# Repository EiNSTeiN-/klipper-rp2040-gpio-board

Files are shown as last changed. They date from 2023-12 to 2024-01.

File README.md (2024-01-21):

# Klipper RP2040 GPIO board

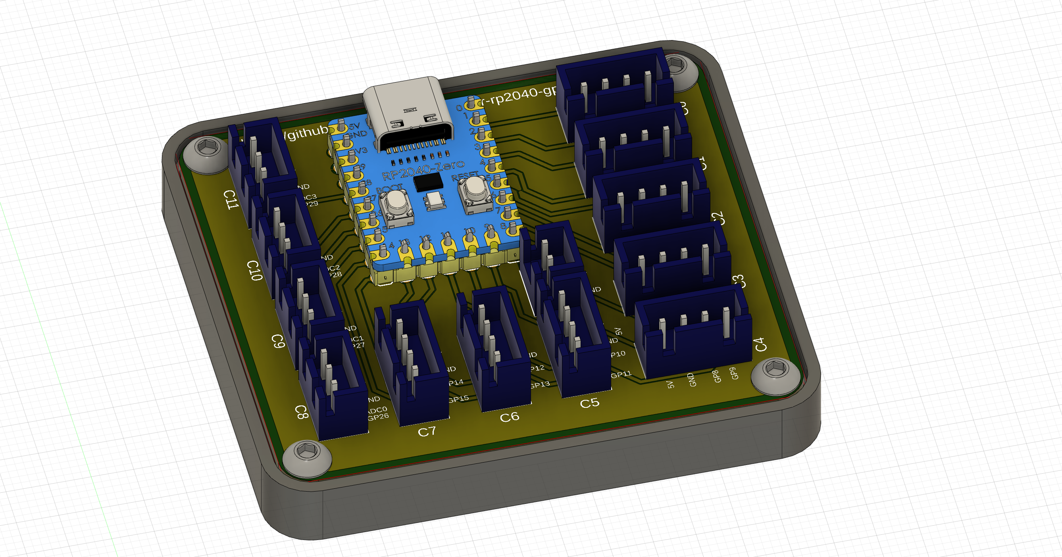
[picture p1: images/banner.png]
CAD Preview


This is a small board that makes it convenient to connect additional sensors to your 3D printer running klipper, based on [RP2040-Zero](https://www.waveshare.com/wiki/RP2040-Zero). It exposes all available analog pins to 4-pin JST-XH headers, and digital pins to 3-pin JST-XH headers.

Features:
* Up to 20 analog pins (buttons, encoders, etc)
* Up to 4 digital pins (servos, hall sensors, thermistors, etc)
* 2 x SPI bus available
* 2 x I2C bus available

## BOM

| Name | Quantity | Description |
|---|---|---|
| PCB | 1 | Order online from your favorite PCB supplier (PCBWay, JLCPCB, etc). |
| RP2040-Zero | 1 | From [Waveshare](https://www.waveshare.com/rp2040-zero.htm) (also available on Aliexpress).
| JST-XH 4-pin | 8 | |
| JST-XH 3-pin | 4 | |
| JST-XH 2-pin | 1 | |
| M3 x heat set insert | 4 | Optional, only needed for the case. |
| M3 x 6mm | 4 | BHCS or SHCS screws. Optional, only needed for the case. |
| Case_bottom.stl | 1 | Optional, print if needed. |

## Klipper installation

Compile Klipper for the RP2040 board. The commands below are intended to be run on your printer host:
```sh
git clone --depth 1 --single-branch https://github.com/Klipper3d/klipper.git ~/klipper-rp2040-gpio
cd ~/klipper-rp2040-gpio
~/klippy-env/bin/python scripts/make_version.py `hostname`
# v0.11.0-146-ge2d7c598-mainsailos
make menuconfig
#                 Klipper Firmware Configuration
#  [*] Enable extra low-level configuration options
#      Micro-controller Architecture (Raspberry Pi RP2040)  --->
#      Bootloader offset (No bootloader)  --->
#      Flash chip (W25Q080 with CLKDIV 2)  --->
#      Communication interface (USB)  --->
#      USB ids  --->
#  ()  GPIO pins to set at micro-controller startup
make -j4
#   (...lots of output...)
#   Creating uf2 file out/klipper.uf2
ls -alh /dev/serial/by-id/usb-*
# lrwxrwxrwx 1 root root 13 Dec 18 15:53 /dev/serial/by-id/usb-RPI_rp2040_E66130100F5E3838-if00 -> ../../ttyACM1
make flash FLASH_DEVICE=/dev/serial/by-id/usb-RPI_rp2040_E66130100F5E3838-if00
ls -alh /dev/serial/by-id/usb-Klipper_rp2040*
# lrwxrwxrwx 1 root root 13 Dec 18 15:53 /dev/serial/by-id/usb-Klipper_rp2040_E66130100F5E3838-if00 -> ../../ttyACM1
```

#### Troubleshooting

* Problem: After flashing the board works fine, but after disconnecting/reconnecting the board it does not boot anymore.
* Solution: Run `make menuconfig` and select `Flash chip (GENERIC_03H with CLKDIV 4)`. See [this issue](https://github.com/raspberrypi/pico-sdk/issues/1304).

## Configuration example

Your specific configuration depends on what is connected to the gpio pins. Example of a minimal configuration:

```ini
[mcu rp2040]
# find with: ls -alh /dev/serial/by-id/usb-Klipper_rp2040*
serial: /dev/serial/by-id/usb-Klipper_rp2040_E66130100F5E3838-if00

[neopixel rp2040_rgb]
pin: rp2040:gpio16
#color_order: GRB
initial_GREEN: 1.0

####
# Add sensors below:

[gcode_button my_button]
pin: ~rp2040:gpio4
press_gcode:
  RESPOND TYPE=command MSG='GP4 pressed'

[pwm_tool my_tool]
pin: rp2040:gpio26
```

Pin `gpio16` can only be used as a neopixel since it is soldered to the RP2040-Zero.

Consult [klipper's configuration reference](https://www.klipper3d.org/Config_Reference.html) for information on how to configure specific sensors with klipper.

## Pinout

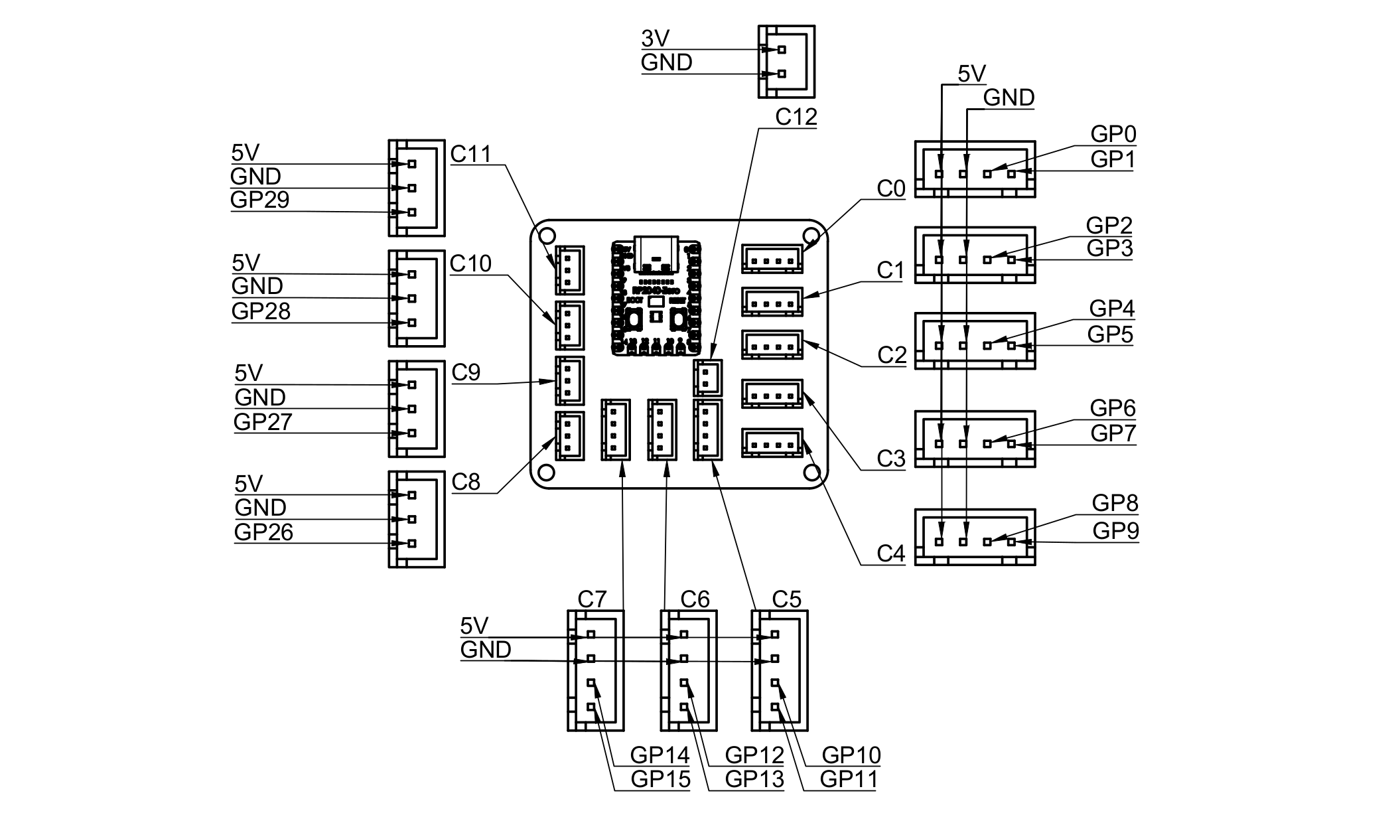
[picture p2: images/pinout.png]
Pinout


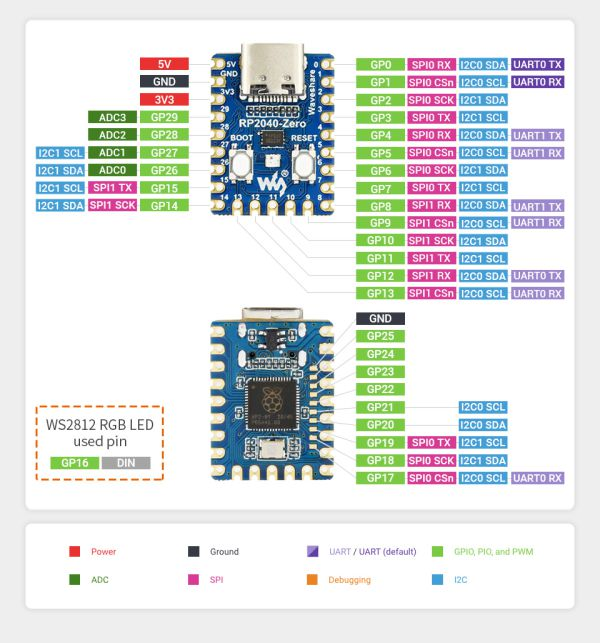
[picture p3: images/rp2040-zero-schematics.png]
RP2040 pinout


For more information, see [RP2040-Zero Wiki](https://www.waveshare.com/wiki/RP2040-Zero).

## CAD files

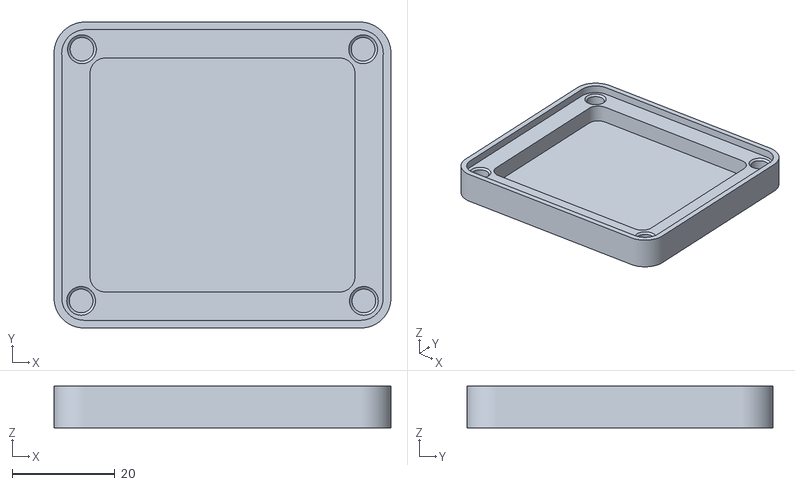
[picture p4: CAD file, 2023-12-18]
STL/Case_Bottom.stl
65.6 x 59.5 x 8.10

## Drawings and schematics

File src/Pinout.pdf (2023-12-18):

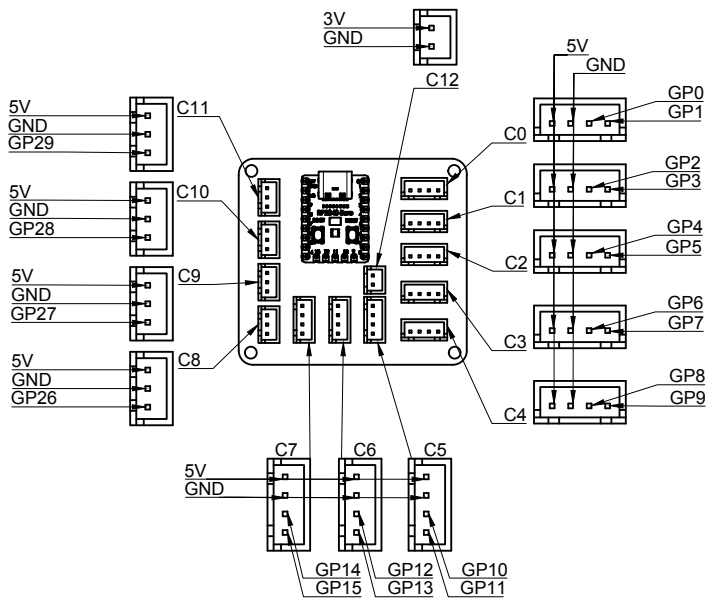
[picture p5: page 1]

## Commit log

2023-12-18 Initial release
    [Case_Bottom.stl]
2023-12-18 Add info on clkdiv 4 issue encountered on some boards
2024-01-20 Use "make flash" from klipper for simpler flashing
2024-01-21 Fix device name
